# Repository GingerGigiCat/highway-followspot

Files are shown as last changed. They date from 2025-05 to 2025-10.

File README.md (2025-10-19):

# HIGHLIGHT!

## Highlight is my followspot i've designed for hack club's [highway](https://highway.hackclub.com/) hardware event



A **followspot** is a type of spotlight used in theatre which is manually controlled and pointed at an actor. They normally have brightness and zoom controls, which mine has!

It has:

- An over 100W white LED COB chip for over 17000 lumens of light output (Max. 150W, real max depends on how much heat the led dissipates as i'll have to limit it so it can't overheat and die)
- An upcycled camera lens no longer good enough for photography but perfect for a beam of light
- Motorised lens control with manual control if desired and zoom recall
- Digital constant current LED dimming (so no flickering from PWM)
- USB-C for computer control of brightness and zoom
- Fully open source everything
- 3 programmable buttons and a fader
- Automatic brightness reduction if the LED gets too hot
- A light on the control panel to give feedback, like if the main LED is too hot or the lens is being pushed too far

The body is 3D printed in PETG but it could be made out of a better material if you feel like it, and the legs are plywood, and of course the lens is glass.

Here's the onshape link! https://cad.onshape.com/documents/9e98bdcd2562c04de815ecc5/w/89c7868c82d5394c068b4491/e/8808e6d7c01ac629712aeab9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

## Why?

I wanted my GCSE Design and Technology project to be a spotlight, but my DT teacher said no and told me to downsize it to a desk lamp. It got me a good grade, but it's not what I wanted to make, so I'm taking the opportunity to make what I want to make, with an LED bright enough to blind my DT teacher! (/j....) I'm going to take inspiration from my project, as I do like the general hexagonal design of it (see below)

PXL_20250429_132238411 MP

I have a passion for the technical parts of theatre, so making this was rather an obvious choice for me

## PCB

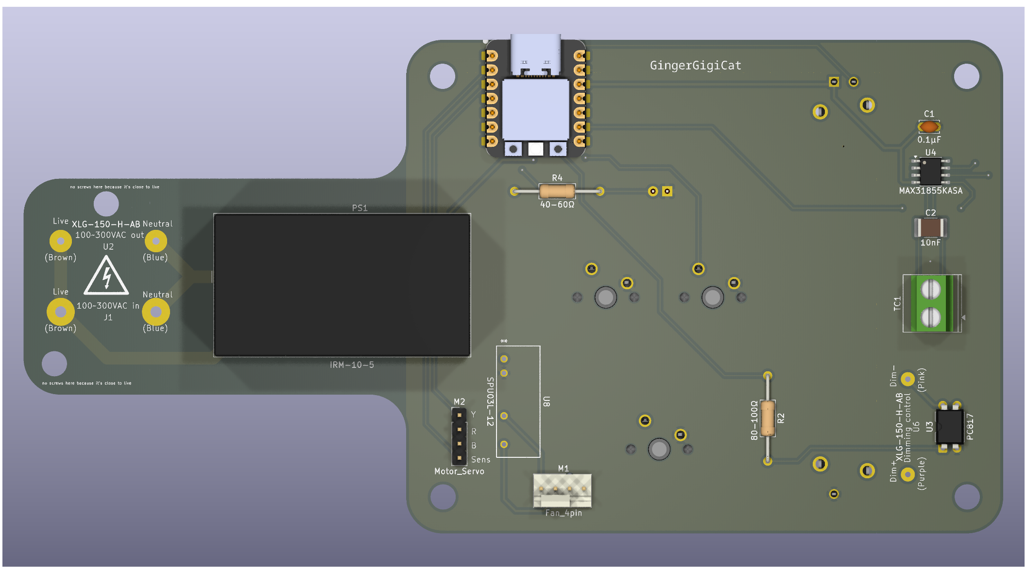
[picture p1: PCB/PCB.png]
PCB


## Wiring Diagram

(Made in GIMP :))

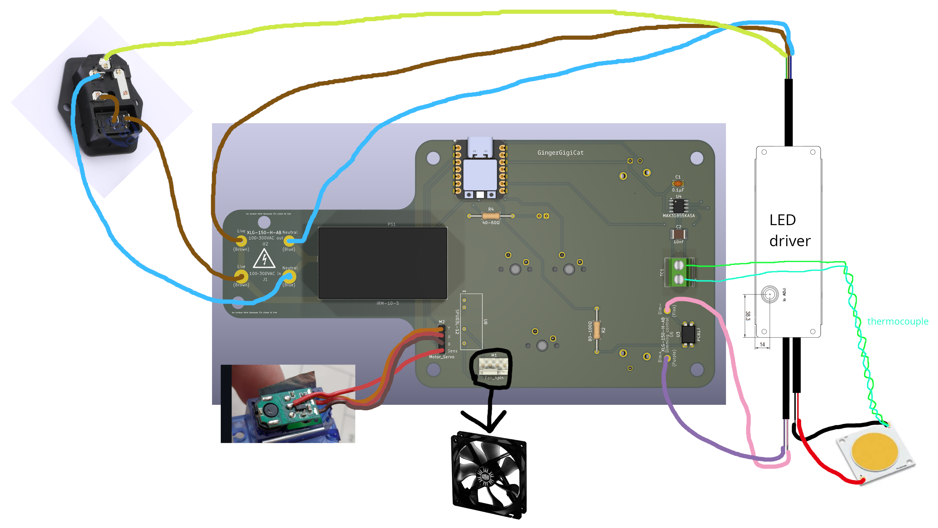
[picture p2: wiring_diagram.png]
wiring_diagram


## More pictures :)







overview_image_267752774_635424

# Bill of Materials

| Vendor | Name (link) | Description | Price (Digikey With VAT) | Price (Local) | Price (LCSC)  | Price(Other) | Notes |
| --- | --- | --- | --- | --- | --- | --- | --- |
| digikey | [XLG-150-H-AB ](https://www.digikey.co.uk/en/products/detail/mean-well-usa-inc/XLG-150-H-AB/10222586) | 150W 27-56V led driver | £31.04 | | x | | |
| LCSC | [IRM-10-5](https://lcsc.com/product-detail/Power-Module-Power-Supply_MW-MEAN-WELL-Enterprises-IRM-10-5_C2857903.html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) | 10W 5V psu | x 6.38 | | $4.32 | | |
| digikey | [SPU03L-12](https://www.digikey.co.uk/en/products/detail/mean-well-usa-inc/SPU03L-12/7707058) | 3W 5v to 12v conerter | £4.51 | | | | |
| digikey | [‎CXM-32-50-80-54-AC00-F2-5‎](https://www.digikey.co.uk/en/products/detail/luminus-devices-inc/CXM-32-50-80-54-AC00-F2-5/5811014) | 50-56V up to 200W LED | £21.78 | | x | | |
| digikey | [K104K15X7RF5TL2](https://www.digikey.co.uk/en/products/detail/vishay-beyschlag-draloric-bc-components/K104K15X7RF5TL2/286538) | 0.1uF tht capacitor | £0.22 | | | | |
| digikey | ["885012210006"](https://www.digikey.co.uk/en/products/detail/w%C3%BCrth-elektronik/885012210006/5453247) | 10nF smt capacitor | £0.46 | | | | |
| digikey | [PTA6043-2010CIB502](https://www.digikey.co.uk/en/products/detail/bourns-inc/PTA6043-2010CIB502/3781226) | 5K slide potentiometer | £1.70 | | x? | | |
| LCSC | [ETA-G-K-24-200cm](https://lcsc.com/product-detail/Electronic-testing-accessories_ETA-ETA-G-K-24-200cm_C5144202.html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) | 2m K-type thermocouple bare wires | | | $4.56 | | |
| LCSC | [MAX31855KASA+T](https://lcsc.com/product-detail/ADCs-DACs-Special-Purpose_Analog-Devices-Inc-Maxim-Integrated-MAX31855KASA-T_C52028.html) | MAX31855 thermocouple amplifier chip | x 8.28 | | $2.33 | | |
| digikey | [Wuerth elektronik screw pin terminal](https://www.digikey.co.uk/en/products/detail/w%C3%BCrth-elektronik/691137710002/6644051) | Screwy terminal block for 2 pins for thermocouple | £0.32 | | | | |
| digikey | [xiao rp2040](https://www.digikey.co.uk/en/products/detail/seeed-technology-co-ltd/102010428/14672129) | xiao rp2040 microcontroller | £4.15 | | x | | |
| digikey | [PC817X2NSZ9F](https://www.digikey.co.uk/en/products/detail/sharp-socle-technology/PC817X2NSZ9F/7942022) | pc817 optocoupler/optoisolator | £0.24 | | x $0.38=£0.28 | | (LCSC minimum order quantity is 5, for just one it would be $0.07 but alas) |
| | | 40 ohm resistor for led | (I have already) | | | £0.05 | (estimate price) |
| | | Red led | (I have already) | | | ~5p if you buy? | |
| | | 80-100 ohm resistor for optocoupler | (will get locally) | | | £0.05 | (estimate price) |
| | | 3x cherry style keyboard switches and keycaps | (I have already) | | | ~5p if you buy? | |
| | | 2.5A fuse - possibly 5x20mm | (will get locally) | | | £0.10 | (estimate price) |
| | | SG90 servo motor | (I have already) | | | | |
| LCSC | [Legion RT-C14B-H1+SS11-1BB](https://lcsc.com/product-detail/AC-Power-Connectors_Legion-RT-C14B-H1-SS11-1BB_C22379821.html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) | iec panel mount input with fuse and switch integrated | x 1.45 | | $1.46 | | LCSC one has a switch too! |
| digikey | [xiao pin headers](https://www.digikey.co.uk/en/products/detail/seeed-technology-co-ltd/102010490/19176770) | 7 pin headers for xiao rp2040, as well as for the servo | £0.22 | (might get locally) | | | |
| digikey | [molex 47053-1000](https://www.digikey.co.uk/en/products/detail/molex/0470531000/2421261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) | 4 pin fan header | £0.43 | | x | | |
| digikey | [ATS-HP-F9L200S70W-014](https://www.digikey.co.uk/en/products/detail/advanced-thermal-solutions-inc/ATS-HP-F9L200S70W-014/5049697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) | 200mm long 10.5mm wide ~60W heat pipe - 3 OF THEM | £12.90 | | | | |
| amazon | [1kg sunlu black petg filament](https://www.amazon.co.uk/SUNLU-Filament-Tangle-Free-Dimensional-Accuracy/dp/B0D1KC72YP) | 1kg black PETG sunlu filament, for more heat resistance | | | | £8.75 | (i'm splitting the cost with a friend so i only get 1kg and pay £8.75 for it, normally it would be about £12) |
| vinted | [Cooler master hyper 212 evo](https://www.vinted.co.uk/items/6787848360-coolmasters-hyper-212-fan) | heatsink with fan | | | | £9.71 |(previously fb marketplace but the one i was going to get sold) |
| amazon | [10g Silicone EC360 Thermal Glue](https://www.amazon.co.uk/EC360%C2%AE-Glue-Thermal-Adhesive-Liquid/dp/B00XQ9AZ8Y) | Thermally conductive adhesive for attaching heat pipes | | | | £5.99 | |
| | | 50x85mm 3mm mdf | | | | free | |
| | | about 40 m4 bolts and nuts (12mm long mostly but some might be longer) | | | | £6 | (estimate price) |
| | | 2 m10 bolts and nuts | | | | £6.00 | |
| | | about 400x200mm of thick plywood | | | | free | |
| JLCPCB | | The pcb!!! | | | | £12.00 | |
| | | | | | | | |
| | | | | | | | |
| | | | | | $12.45 | | Just parts cost |
| shipping stuff | | | | | $10.40 | | Shipping cost |
| Total | | | £78.18 | | $22.85=£16.73 | £48.94 | £144.25 |
| | | | | | cheaper! | | |
| Total total | (manual value input) | | | | | | $195.39 |

(I am willing to cover the amount i've gone over budget if i have to)

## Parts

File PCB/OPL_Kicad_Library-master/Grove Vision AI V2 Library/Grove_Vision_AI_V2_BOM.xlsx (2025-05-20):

Layer Jump | Number | Name | Specification | Operating Temperature | MPN Code | Quantity | Base | Plug Position | Process
N | 301010000 | SMD RES 0R-5%-1/16W;0402 |  | -55°C to 155°C | RC0402JR-070RL | 3 | 1 | R29,R30,R39 | SMT1
N | 301010004 | SMD RES 10K-5%-1/16W;0402 |  | -55°C to 155°C | RC0402JR-0710KL | 7 | 1 | R5,R7,R8,R23,R24,R31,R38 | SMT1
N | 301010008 | SMD RES 510K-5%-1/16W;0402 |  | -55°C to 155°C | RC0402JR-07510KL | 1 | 1 | R35 | SMT1
N | 301010456 | SMD RES 100K-1%-1/16W;0402 |  | -55°C to 155°C | RC0402FR-07100KL | 7 | 1 | R6,R10,R11,R16,R32,R33,R37 | SMT1
N | 301010495 | SMD RES;5.1K-1%-1/16W;0402 |  | -55°C to 155°C | RC0402FR-075K1L | 3 | 1 | R2,R3,R36 | SMT1
N | 301010746 | SMD RES 2.2K-1%-1/16W;0402 |  | -55°C to 155°C | RC0402FR-072K2L | 10 | 1 | R1,R4,R13,R14,R15,R19,R20,R21,R22,R40 | SMT1
N | 301011331 | SMD RES 22.1K-1%-1/16W;0402 |  | -55°C to 155°C | RC0402FR-0722K1L | 2 | 1 | R26,R34 | SMT1
N | 302010004 | SMD CAP Ceramic 100nF-16V-10%-X7R;0402 |  | -55°C to 125°C | CC0402KRX7R7BB104 | 18 | 1 | C5,C8,C13,C20,C21,C22,C23,C24,C25,C26,C27,C29,C30,C31,C32,C35,C36,C39 | SMT1
N | 302010006 | SMD CAP Ceramic 10nF-50V-10%-X7R;0402 |  | -55°C to 125°C | CC0402KRX7R9BB103 | 1 | 1 | C3 | SMT1
N | 302010049 | SMD CAP Ceramic 12pF-50V-5%-NPO;0402 |  | -55°C to 125°C | CC0402JRNPO9BN120 | 2 | 1 | C14,C15 | SMT1
N | 302010051 | SMD CAP Ceramic 220nF-16V-10%-X7R;0402 |  | -55°C to 125°C | CC0402KRX7R7BB224 | 1 | 1 | C16 | SMT1
N | 302010407 | SMD CAP Ceramic 4.7uF-10V-10%-X5R;0402 |  | -55°C to 85°C | CC0402KRX5R6BB475 | 7 | 1 | C4,C6,C7,C9,C10,C28,C34 | SMT1
N | 302010519 | SMD CAP Ceramic 10uF-10V-20%-X5R;0402 |  | -55°C to 85°C | CC0402MRX5R6BB106 | 2 | 1 | C11,C37 | SMT1
N | 302013249 | SMD CAP Ceramic 1uF-10V-10%-X5R;0402 |  | -55°C to 85°C | CL05A105KP5NNNC | 5 | 1 | C1,C2,C17,C18,C19 | SMT1
N | 303010544 | SMD Inductor 4.7uH-20%-1.1A;0806 |  | -40°C to 105°C | VLS201610HBX-4R7M-1 | 1 | 1 | L1 | SMT1
N | 303011858 | SMD Inductor 470nH-20%-2.6A;0603 |  | -40°C to 125°C | TFM160808ALC-R47MTAA | 2 | 1 | L2,L3 | SMT1
N | 304011053 | SMD Diode Schottky 40V-1A;SOD-323 |  |  | B5819WS SL | 4 | 1 | D1,D2,D3,D4 | SMT1
N | 304090121 | SMD LED Clear-Green;0402 | As posted |  | BL-HGE37A-AV-TRB | 1 | 1 | LED2 | SMT1
N | 304090746 | SMD LED Clear-Yellow;0402 | As posted |  | 16-213/Y2C-AN2Q1B/3T | 1 | 1 | LED1 | SMT1
N | 305030071 | SMD MOSFET N-CH 20V-500mA;SOT-523 |  |  | CJ1012 | 5 | 1 | Q1,Q2,Q3,Q4,Q5 | SMT1
N | 306011444 | SMD Crystal;24MHz-12pF-10ppm-4P-2.0*1.6*0.5mm |  | -40°C to 85°C | Y2400FE001 | 1 | 1 | X1 | SMT1
N | 310011697 | SMD IC MCU;Dual Cortex-M55 Core(Max 400MHz)-With a 400MHz NPU;WLCSP-65 | L5.58*W2.27mm | -40°C to 85°C | HX6538-A01TWA | 1 | 1 | U1 | SMT1
N | 310032794 | SMD IC PMIC;DCDC Buck-ADJ-2.2MHz-4A;DFN1.5×1.5-6 |  | -40°C to 85°C | SY80004DQD | 2 | 1 | U4,U6 | SMT1
N | 310032813 | SMD IC PMIC;LDO-1.8V-300mA;XTDFN-1*1-4L |  | -40°C to 125°C | SGM2036S-1.8XXDH4G/TR | 1 | 1 | U3 | SMT1
N | 310071431 | SMD IC Interface USB to High Speed TTL;QFN16 | USB to High-Speed Serial Port | -40°C to 85°C | CH343P | 1 | 1 | U2 | SMT1
N | 310091468 | SMD IC Memory;128Mbit-1.8V;SOIC-8 |  | -40°C to 85°C | W25Q128JWSIQ | 1 | 1 | U5 | SMT1
N | 311020009 | SMD Top Button 4N;4P-L4.6*W3.2*H2.5mm |  | -20°C to 70°C | SKRPADE010 | 1 | 1 | RST1 | SMT1
N | 311020518 | SMD Top Button 1.57N;4P-L4.6*W3.2*H2.5mm |  | -30°C to 85°C | SKRPABE010 | 1 | 1 | BOOT1 | SMT1
N | 312030502 | SMD DIGITAL MIC OMNI -26dBFS;OCLGA-4:3.5*2.65*0.94mm |  | -40˚C to 100˚C | MSM261D3526H1CPM | 1 | 1 | MIC1 | SMT1
N | 319015667 | PCB;Grove - Vision AI Module V2 -蓝油白字-4层 | 20*40*1.6mm-ENIG-FR4;Steel mesh code；404012305 |  |  | 1 | 1 |  | SMT1
N | 320011358 | SMD USB TYPE C-W/P;12+4P-8.94*7.35*3.26mm |  | -30°C to 85°C | USB-31C-F-16P-L7.35 | 1 | 1 | J1 | SMT1
N | 320031231 | DIP Black Female Header VERT;1*7P-2.54-5.0mm |  | -40℃ to 105℃ |  | 2 | 1 | P8,P9 | Unit
N | 320060904 | SMD FPC CONN Bottom Contact;15P-1.0mm;L19.9*W6.76*H2.0mm |  | -30°C to 85°C | ST-FPC-W102015-D | 1 | 1 | J2 | SMT1
N | 320090535 | SMD uSD Card Holder;9+4P-L11.25*W6.96*H1.42mm |  | -25°C to 70°C | ST-TF-MR267 | 1 | 1 | J5 | SMT1
N | 320110032 | SMD Grove Female Header-Beige;4P-2.0-90D | 2.0-4PHorizontal Mount with Locking Socket |  | PHS-4A horizontal mount | 1 | 1 | J3 | SMT1

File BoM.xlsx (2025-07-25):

Vendor | Name (link) | Description | Price (Digikey With VAT) | Price (Local) | Price (LCSC) | Price(Other) | Notes
~~digikey~~ | ~~ELG-150-54B~~ (https://www.digikey.co.uk/en/products/detail/mean-well-usa-inc/ELG-150-54B/7702975) | ~~150W 54V led driver~~ | ~~x 37.94~~ |  | ~~x~~ |  | ~~BACKORDER NEEDS BUYING, LEAD TIME CURRENTLY 13/06/2025~~
digikey | XLG-150-H-AB (https://www.digikey.co.uk/en/products/detail/mean-well-usa-inc/XLG-150-H-AB/10222586) | 150W 27-56V led driver | £31.04 |  | x
LCSC | IRM-10-5 (https://www.digikey.co.uk/en/products/detail/mean-well-usa-inc/IRM-10-5/7704657) | 10W 5V psu | x 6.38 |  | $4.32 (https://lcsc.com/product-detail/Power-Module-Power-Supply_MW-MEAN-WELL-Enterprises-IRM-10-5_C2857903.html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)
~~digikey~~ | ~~SMU02L-12~~ (https://www.digikey.co.uk/en/products/detail/mean-well-usa-inc/SMU02L-12/7706871) | ~~2W 5v to 12v converter~~ | ~~x 3.54~~ |  | ~~x?~~
digikey | SPU03L-12 (https://www.digikey.co.uk/en/products/detail/mean-well-usa-inc/SPU03L-12/7707058) | 3W 5v to 12v conerter | £4.51
digikey | L2C5-40801825G3200 (https://www.digikey.co.uk/en/products/detail/lumileds/L2C5-40801825G3200/7344822) | 51.7V ~116W LED | £34.15 |  | x
~~digikey~~ | ~~Schurter OGN Fuse holder~~ (https://www.digikey.co.uk/en/products/detail/schurter-inc/0031-8211/669926) | ~~5x20mm fuse holder~~ | ~~x 1.04~~ |  | ~~x?~~
digikey | K104K15X7RF5TL2 (https://www.digikey.co.uk/en/products/detail/vishay-beyschlag-draloric-bc-components/K104K15X7RF5TL2/286538) | 0.1uF tht capacitor | £0.22
digikey | "885012210006" (https://www.digikey.co.uk/en/products/detail/w%C3%BCrth-elektronik/885012210006/5453247) | 10nF smt capacitor | £0.46
digikey | PTA6043-2010CIB502 (https://www.digikey.co.uk/en/products/detail/bourns-inc/PTA6043-2010CIB502/3781226) | 5K slide potentiometer | £1.70 |  | x?
~~digikey~~ | ~~240-080~~ (https://www.digikey.co.uk/en/products/detail/digilent-inc/240-080/5418219) | ~~1m K-type thermocouple bare wires~~ | ~~x 8.86~~ |  | ~~x~~
LCSC | ETA-G-K-24-200cm (https://lcsc.com/product-detail/Electronic-testing-accessories_ETA-ETA-G-K-24-200cm_C5144202.html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) | 2m K-type thermocouple bare wires |  |  | $4.56 (https://lcsc.com/product-detail/Electronic-testing-accessories_ETA-ETA-G-K-24-200cm_C5144202.html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)
LCSC | MAX31855KASA+T (https://www.digikey.co.uk/en/products/detail/analog-devices-inc-maxim-integrated/MAX31855KASA-T/2591213) | MAX31855 thermocouple amplifier chip | x 8.28 |  | $2.33 (https://lcsc.com/product-detail/ADCs-DACs-Special-Purpose_Analog-Devices-Inc-Maxim-Integrated-MAX31855KASA-T_C52028.html)
digikey | Wuerth elektronik screw pin terminal (https://www.digikey.co.uk/en/products/detail/w%C3%BCrth-elektronik/691137710002/6644051) | Screwy terminal block for 2 pins for thermocouple | £0.32
digikey | xiao rp2040 (https://www.digikey.co.uk/en/products/detail/seeed-technology-co-ltd/102010428/14672129) | xiao rp2040 microcontroller | £4.15 |  | x
digikey | PC817X2NSZ9F (https://www.digikey.co.uk/en/products/detail/sharp-socle-technology/PC817X2NSZ9F/7942022) | pc817 optocoupler/optoisolator | £0.24 |  | x $0.38=£0.28 |  | (LCSC minimum order quantity is 5, for just one it would be $0.07 but alas)
 |  | 40 ohm resistor for led | (I have already) |  |  | £0.05 | (estimate price)
 |  | Red led | (I have already) |  |  | ~~~5p if you buy?~~
 |  | 80-100 ohm resistor for optocoupler | (will get locally) |  |  | £0.05 | (estimate price)
 |  | 3x cherry style keyboard switches and keycaps | (I have already) |  |  | ~~~5p if you buy?~~
 |  | 2.5A fuse - possibly 5x20mm | (will get locally) |  |  | £0.10 | (estimate price)
 |  | SG90 servo motor | (I have already)
LCSC | DAC-13F (https://www.digikey.co.uk/en/products/detail/dit/DAC-13F/18681314) | iec panel mount input with fuse integrated | x 1.45 |  | $1.46 (https://lcsc.com/product-detail/AC-Power-Connectors_Legion-RT-C14B-H1-SS11-1BB_C22379821.html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) |  | LCSC one has a switch too!
digikey | xiao pin headers (https://www.digikey.co.uk/en/products/detail/seeed-technology-co-ltd/102010490/19176770) | 7 pin headers for xiao rp2040, as well as for the servo | £0.22 | (might get locally)
digikey | molex 47053-1000 (https://www.digikey.co.uk/en/products/detail/molex/0470531000/2421261) | 4 pin fan header | £0.43 |  | x
digikey | ATS-HP-F9L200S70W-014 (https://www.digikey.co.uk/en/products/detail/advanced-thermal-solutions-inc/ATS-HP-F9L200S70W-014/5049697) | 200mm long 10.5mm wide ~60W heat pipe - 3 OF THEM | £12.90
~~AMAZON~~ | ~~1kg Creality Black PETG filament~~ (https://www.amazon.co.uk/Creality-PETG-Filament-1-75-Printer/dp/B0DZVWW11M) | ~~1kg black PETG creality filament, i need it for the better heat resistance~~ |  |  |  | ~~x 12.99~~ (https://www.amazon.co.uk/Creality-PETG-Filament-1-75-Printer/dp/B0DZVWW11M)
amazon | 1kg sunlu black petg filament (https://www.amazon.co.uk/SUNLU-Filament-Tangle-Free-Dimensional-Accuracy/dp/B07TJDTJZD) | 1kg black PETG sunlu filament, for more heat resistance |  |  |  | £8.75 (https://www.amazon.co.uk/SUNLU-Filament-Tangle-Free-Dimensional-Accuracy/dp/B0D1KC72YP) | (i'm splitting the cost with a friend so i only get 1kg and pay £8.75 for it, normally it would be about £12)
fb marketplace | Cooler master hyper 212 evo (https://www.facebook.com/marketplace/item/1101663772011711) | heatsink with fan |  |  |  | £10.00
amazon | 10g Silicone EC360 Thermal Glue (https://www.amazon.co.uk/EC360%C2%AE-Glue-Thermal-Adhesive-Liquid/dp/B00XQ9AZ8Y) | Thermally conductive adhesive for attaching heat pipes |  |  |  | £5.99
 |  | 50x85mm 3mm mdf |  |  |  | free
 |  | about 40 m4 bolts and nuts (12mm long mostly but some might be longer) |  |  |  | £6 | (estimate price)
 |  | 2 m10 bolts and nuts |  |  |  | £6.00
 |  | about 400x200mm of thick plywood |  |  |  | free
JLCPCB |  | The pcb!!! |  |  |  | £12.00
 |  |  |  |  | $12.45 |  | Just parts cost
shipping stuff |  |  |  |  | $10.40 |  | Shipping cost
Total |  |  | £90.34 |  | $22.85=£16.73 | £48.94 | £156.01
 |  |  |  |  | cheaper!
Total total | (manual value input) |  |  |  |  |  | $209.51

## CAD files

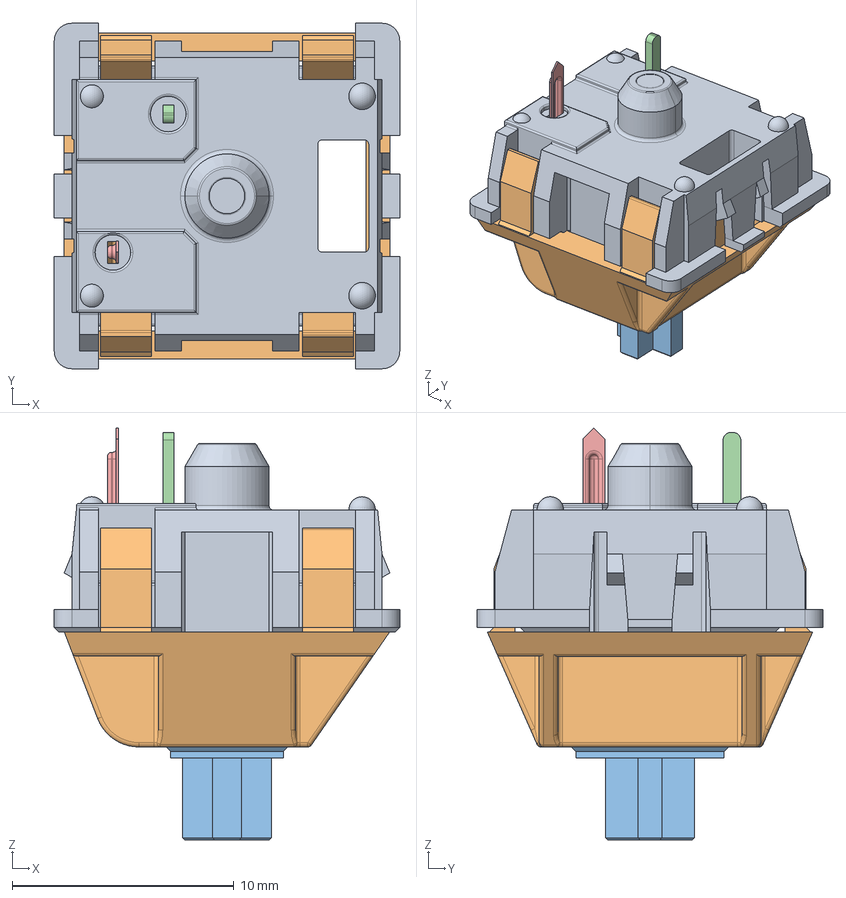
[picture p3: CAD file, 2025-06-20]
PCB/3d_models/cherry_switch.stp
15.6 x 15.6 x 18.6 mm
MX_DOWN
MX_UP
UP_MX
MX_PIN
MX_SPRING
MX_CLICK

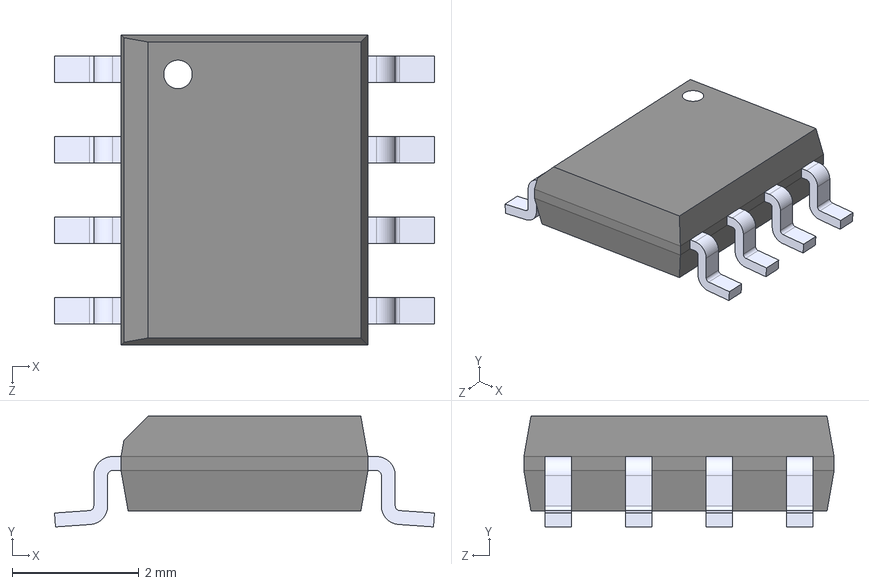
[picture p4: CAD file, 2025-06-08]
PCB/MAX6675/MAX6675.step
6.00 x 1.75 x 4.90 mm

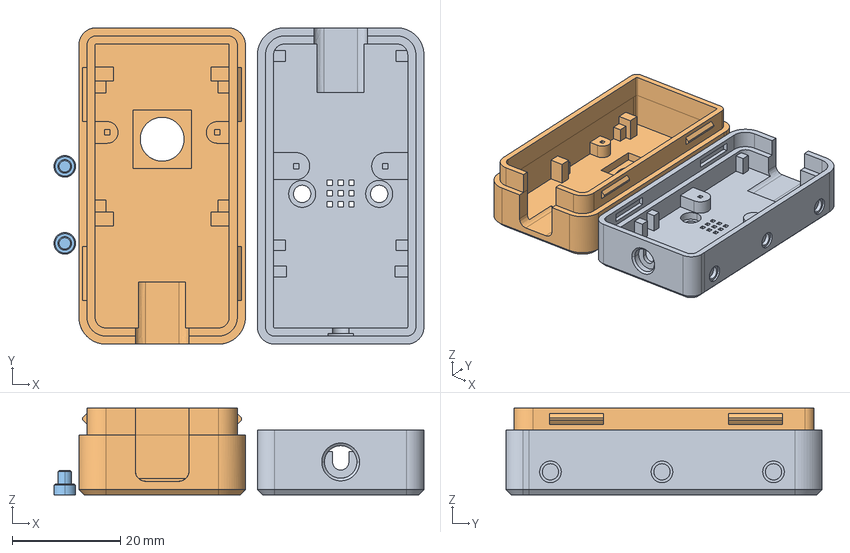
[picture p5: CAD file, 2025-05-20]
PCB/OPL_Kicad_Library-master/Grove Vision AI V2 Library/himax.stp
68.4 x 58.5 x 16.1 mm

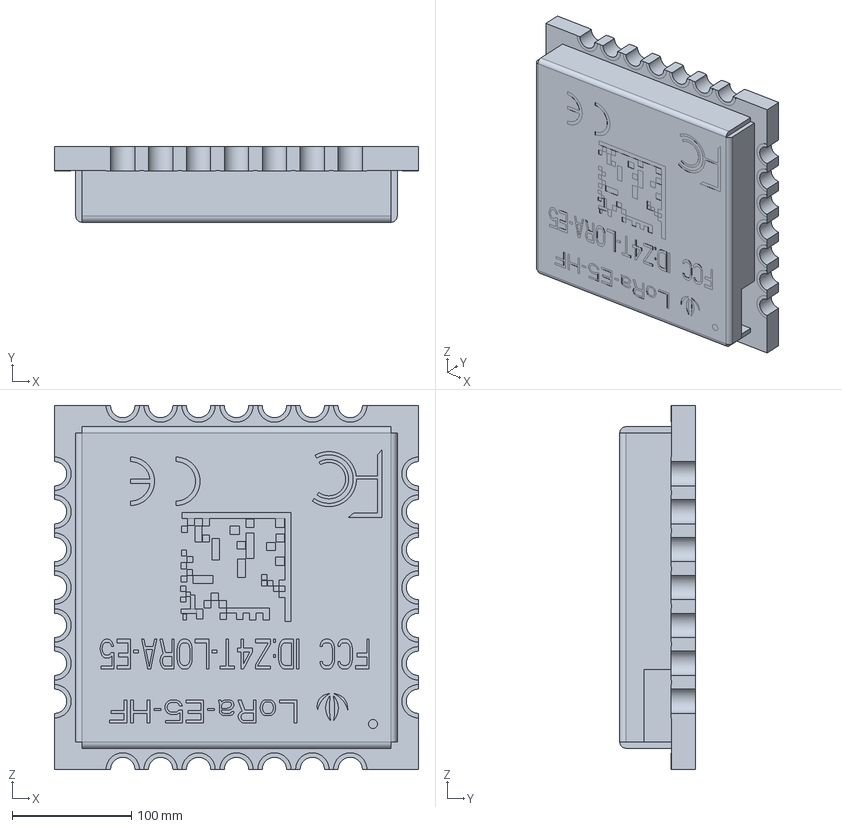
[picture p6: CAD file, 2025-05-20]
PCB/OPL_Kicad_Library-master/Seeed Studio Wio Series/Wio-E5-LE/LoRa-E5-LE-HF_3D_File.stp
304.8 x 63.8 x 304.8 mm

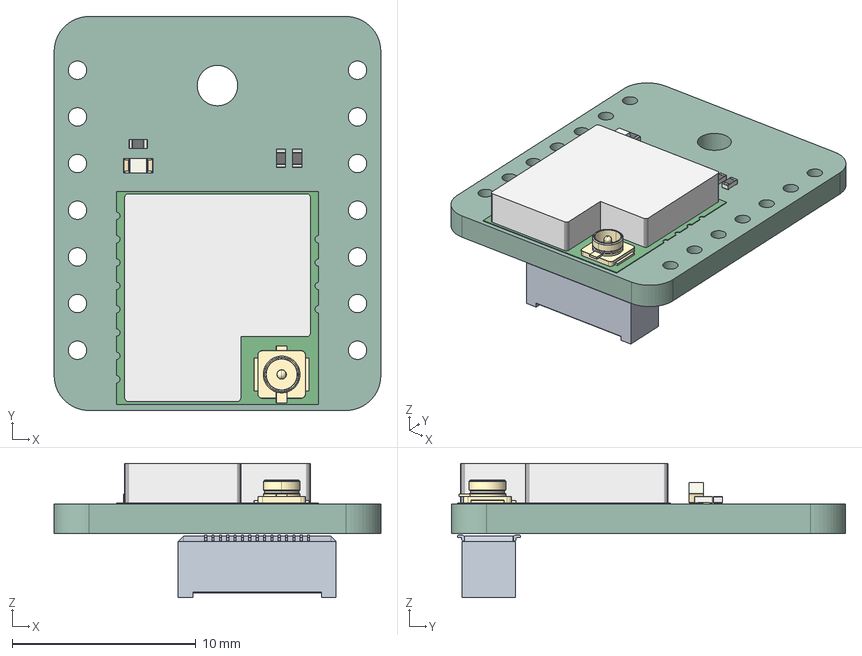
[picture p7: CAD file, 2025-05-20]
PCB/OPL_Kicad_Library-master/Seeed Studio Wio Series/Wio-SX1262/Wio-SX1262_for_XIAO_3D_file.step
17.8 x 21.4 x 7.30 mm
R_0402_1005Metric x 3
LED_0603_1608Metric
PCB
BF04-30pin-35H
Wio-SX1262 for XIAO V1.0_PCB

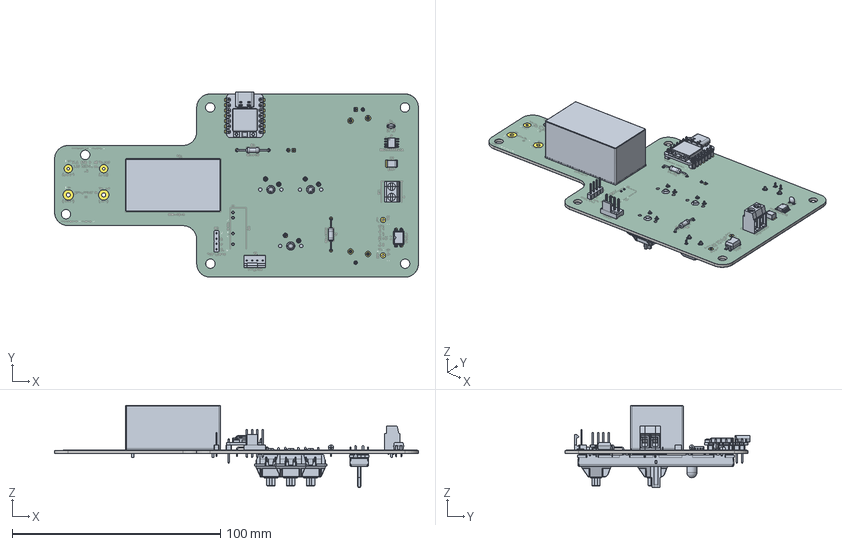
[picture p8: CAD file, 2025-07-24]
PCB/PCB.step
174.8 x 89.0 x 39.5 mm
SOIC-8_3.9x4.9mm_P1.27mm
DIP-4_W7.62mm
R_Axial_DIN0207_L6.3mm_D2.5mm_P15.24mm_Horizontal x 2
C_1812_4532Metric
PinHeader_1x04_P2.54mm_Vertical
FanPinHeader_1x04_P2.54mm_Vertical
MRT12P5_SX
MRT12P5_CNT
MRT12P5_DX
power_supply_irm-10-5
C_Disc_D3.4mm_W2.1mm_P2.50mm
7-Pin Header - Male - 2.54mm x 2
MX_DOWN x 3
MX_UP x 3
UP_MX x 3
MX_PIN x 3
MX_SPRING x 3
MX_CLICK x 3
LED_D5.0mm
PCB_copper
PCB_silkscreen
PCB_soldermask
PCB_PCB

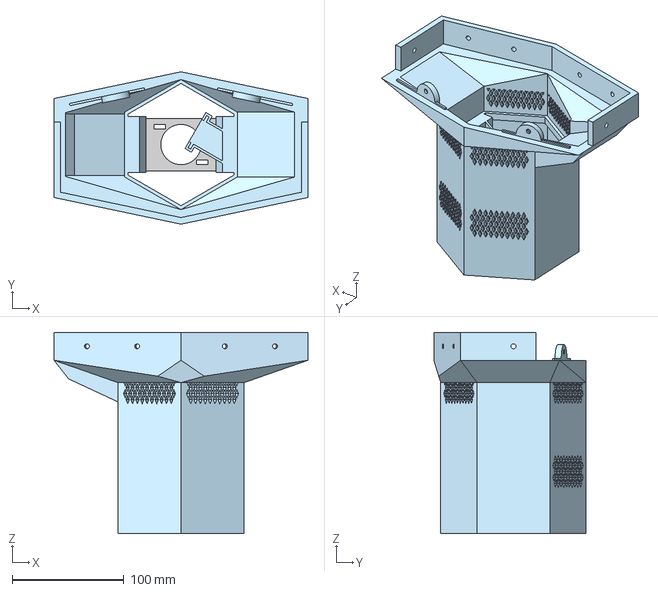
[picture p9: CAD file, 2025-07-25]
Production/3d print parts/Outer Light Tube.step
227.0 x 136.2 x 180.0 mm

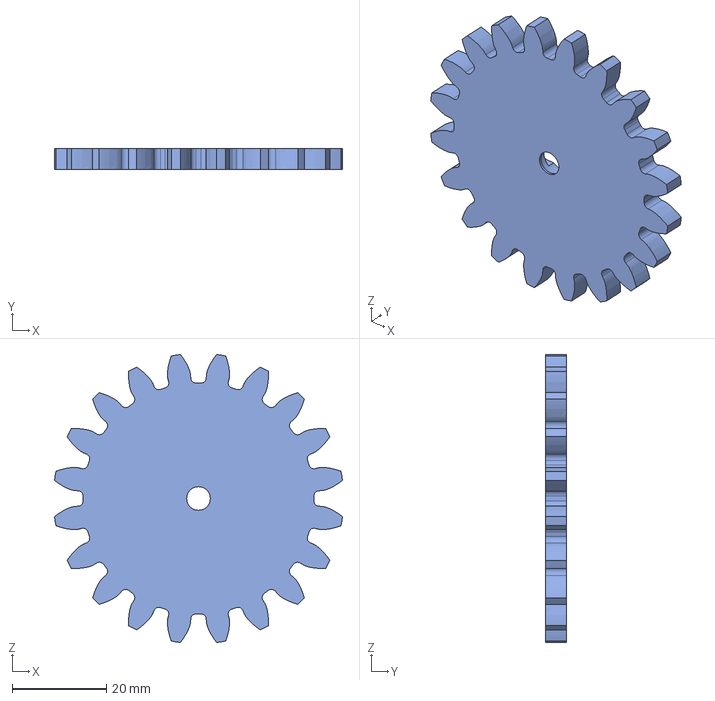
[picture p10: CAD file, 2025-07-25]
Production/3d print parts/Gear.step
61.1 x 4.50 x 61.1 mm

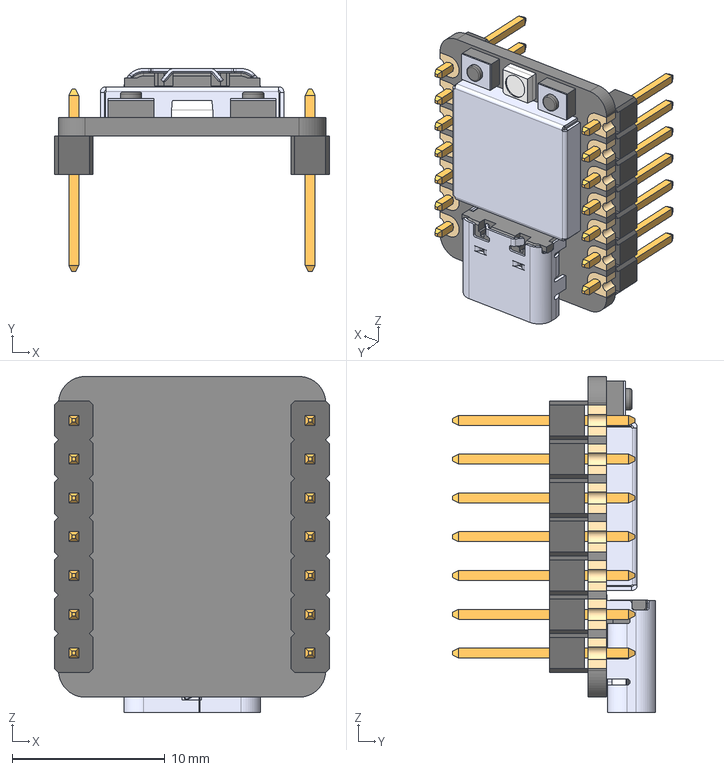
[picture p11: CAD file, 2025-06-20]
PCB/3d_models/xiao rp2040 with pins.step
18.0 x 13.3 x 22.0 mm
7-Pin Header - Male - 2.54mm x 2

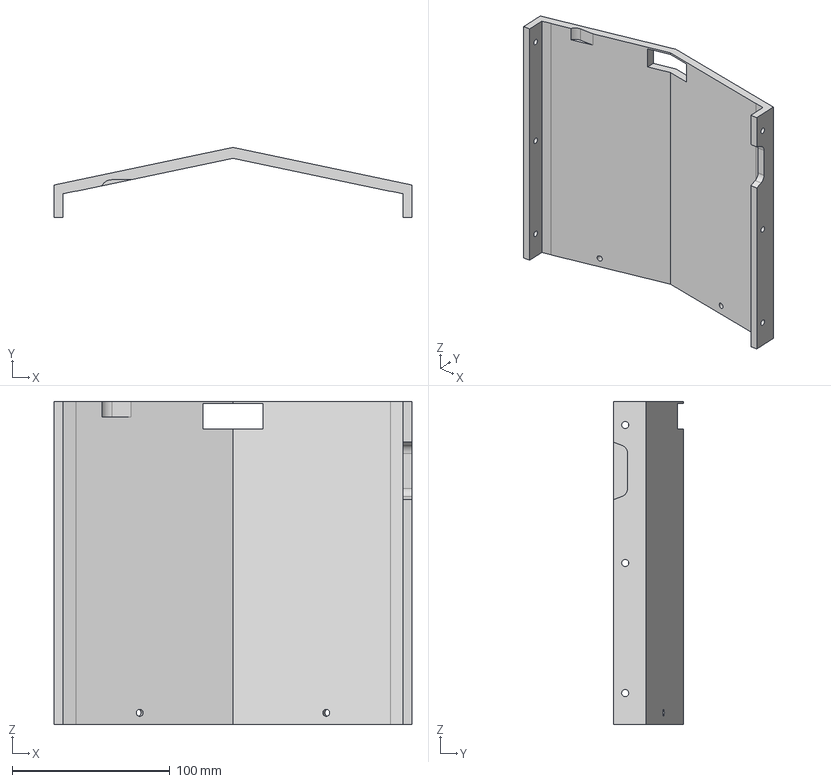
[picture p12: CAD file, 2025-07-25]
Production/3d print parts/electronics box roof.step
227.0 x 44.5 x 205.0 mm

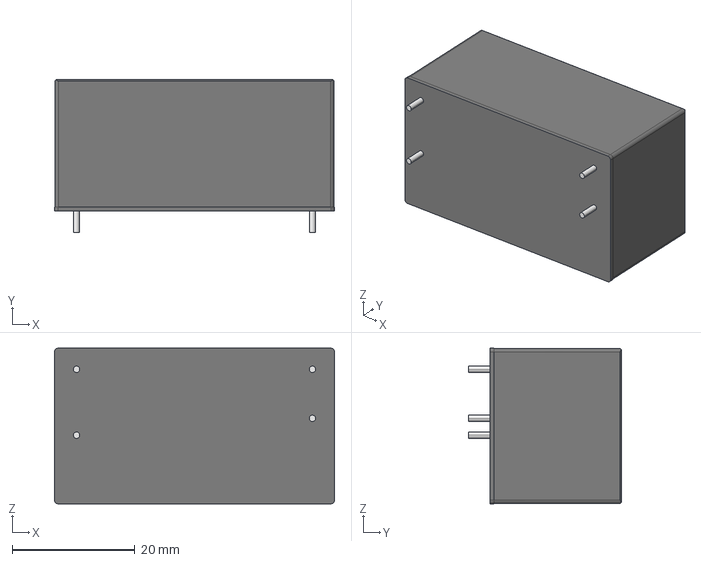
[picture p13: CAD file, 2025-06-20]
PCB/3d_models/power_supply_irm-10-5.stp
45.7 x 25.0 x 25.4 mm

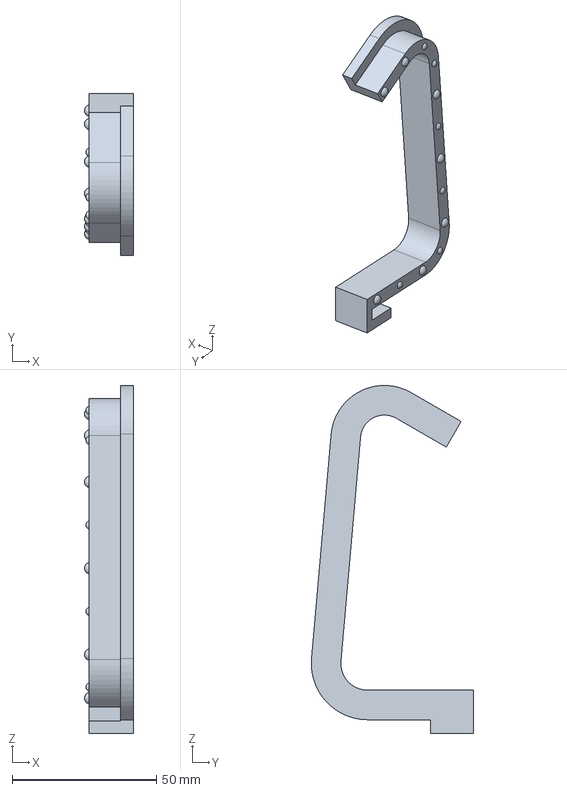
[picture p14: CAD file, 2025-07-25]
Production/3d print parts/pipe bending tool1 part1.step
17.0 x 56.2 x 120.4 mm

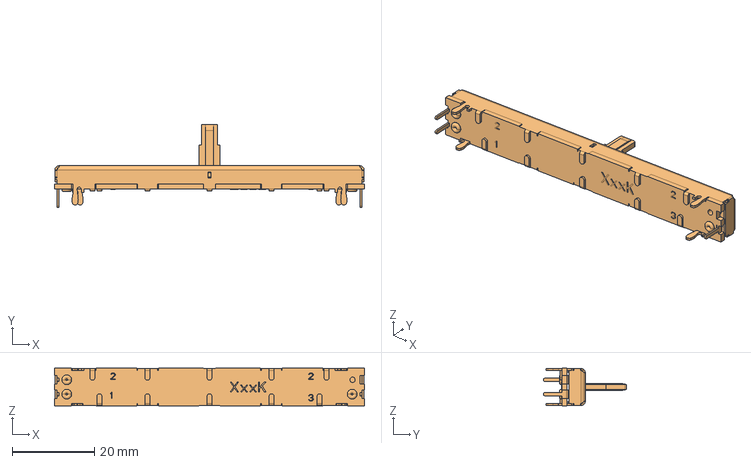
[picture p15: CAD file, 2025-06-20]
PCB/3d_models/pta6043-2x10cixxxx-fader.stp
75.2 x 20.2 x 9.20 mm

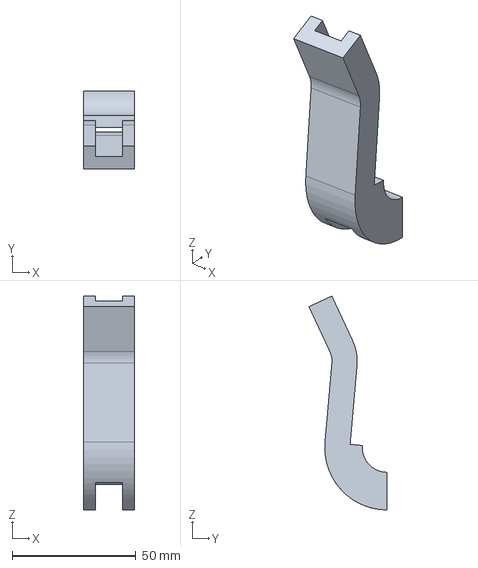
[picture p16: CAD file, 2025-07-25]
Production/3d print parts/pipe bending tool2.step
20.5 x 31.6 x 86.6 mm

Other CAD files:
PCB/3d_models/xiao rp2040 (no pins).STEP
Production/3d print parts/Inner Light Tube.step
Production/3d print parts/leg knob x2.step
PCB/3d_models/691137710002+%28rev1%29 terminal block.stp
PCB/OPL_Kicad_Library-master/Grove Vision AI V2 Library/himax.3mf
Production/3d print parts/Electronics Box.step
Production/3d print parts/Front handle.step
Production/3d print parts/Pinion.step
Production/3d print parts/back panel.step
Production/3d print parts/heatsink bracket x2.step
Production/3d print parts/pipe bending tool1 part2.step

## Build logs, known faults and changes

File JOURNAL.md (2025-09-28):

## Time so far: 3 + 1 + 2.5 + 1.5 + 1 + 3 + 1 + 4 + 2 + 1 + 1.5 + 3 + 3.5 + 0.5 + 0.25 + 1.25 + 4 + 0.5 + 1 + 1.5 + 1 + 1 + 0.5 + 2 + 4 + 1.5 + 2 + 2.5 + 4 + 1 + 2 + 1 + 1.5 + 2 = 65 hours

# Saturday 17 May 2025 - 19:00 - 3 hours

So I've been wanting to make a spotlight for a while. I had planned for my GCSE Design & Technology project to be a spotlight, so I did research including a questionnaire on what people look for in a spotlight, and I upcycled a camera lens which is unsuitable for a camera but it works great to put light through. However, my teacher decided no and told me to make a desk lamp in the style of a spotlight. No lens, no very bright LED, and nothing over 9V. And it got me a good grade, but it's underwhelming and it isn't what I wanted to make.

Therefore, I want to properly go through with designing and creating a real, bright, functioning spotlight, taking inspiration from my desk lamp (the desk lamp is below)

PXL_20250429_132217899 MP
PXL_20250501_122556802 MP

I am also inspired by the [beacon](https://hackclub.slack.com/archives/C0266FRGV/p1723503357605259) that [ruckusmatter](https://hackclub.slack.com/team/U06TZK6EKU6) made during arcade, and i'd like it include a way for my spotlight to have a perfectly straight beam. For reference, the beacon is 17,000 lumens and its colour temperature is 5600k.


Oh also, the 9/11 memorial [Tribute In Light](https://en.wikipedia.org/wiki/Tribute_in_Light) also inspired me

I've been researching LEDs and PSUs. I've been looking on mouser electronics, and I found 2 LEDs that particularly stand out to me.
[One of them](https://www.mouser.co.uk/ProductDetail/Cree-LED/CMB3090-R050-000Q0H0A40G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) is by CREE, a well-known and reliable LED manufacturer, so I should be able to rely on it. This one is 48V, which is nice as it is a rather common voltage, and it produces 12,488 lumens and has a colour temperature of 4000k, which is a more pleasant, warmer shade of white than the spotlight. However, I am unsure about this LED as not only is it less bright than the beacon, it also has some conflicting information as it says  it is 1.2A, but that it is 82W, which can not both be true with a voltage of 48V.

[This other LED](https://www.mouser.co.uk/ProductDetail/Lumileds/L2C5-40801825G3200?qs=T3oQrply3y8Ak6%2FCD8N%252BaQ%3D%3D), by Lumileds seems like it could be better. It is 51.7V at 2.25A and 116W, producing 17,075 lumens, with the same 4000k colour temperature. It should be very bright, however I don't know if it would be the same true light output as the beacon because of the potential for light loss, especially since the lens will have to be a distance away from the light in order to get a straight beam. However, the higher power requirements and weird voltage means finding a suitable power supply may be more difficult.

In terms of powering the LED, I was initially planning to just have a dc power supply of the needed voltage, then allow dimming the LED by using pwm with a MOSFET. I learned that using PWM might not be the best idea though with that much power. Instead a constant current dimmable LED power supply, like [this one](https://www.mouser.co.uk/ProductDetail/MEAN-WELL/ELG-100-48B?qs=n51ddIYULBkC86Em3tr4DQ%3D%3D) from the reputable power supply brand Mean Well. It's got 2 pins which are used for dimming, with 3 options for how to dim the LED. It can be done by: giving it a constant voltage from 0-10V, giving it PWM at 10V, and applying a resistance between the two pins. I'm not sure which of these is the best option, as I don't know of a microcontroller that can produce pwm at 10V, or give a constant variable voltage as high as 10V. This is something I will need to think about.

I would like to have motor controlled zooming of the lens, but I would also like to have the option to control it manually when I want to. For example, it would be great if I could just press a button and have the lens snap into place to give a perfectly straight beam, and be able to save a certain beam angle to repeat later. But also, when manually using it as a followspot, it can be much more convenient and intuitive to physically move a handle which moves the lens. Perhaps I could do this using the same kind of thing as how the extruder on my 3d printer is moved, I think using a belt. It can be moved freely by hand when it's off, but when it's on it is locked in place and I can't move it.

# Monday 19 May 13:00 - 1 hour

I was looking into how I would control the brightness. I was initially thinking I would need 3 power supplies in total, one for the microcontroller, one for the 10V PWM signal, and the LED driver. I thought I would have to use a MOSFET or transistor in order to control the PWM. However I then searched for how to dim a meanwell led driver in particular, and i found [this forum answer](https://electronics.stackexchange.com/a/563669) where they suggest using an optocoupler, which apparently works. An optocoupler is a small box for electrically isolating two circuits, containing an LED and a light dependent resistor. When the LED turns on, the LDR lets current 
 through on the other side. Therefore I can generate a PWM signal for the brightness, and it can go into the optocoupler and from the optocoupler into the dimming pins of the LED driver. I will need to look at the datasheet of the optocoupler I choose, to check the voltage and current needed so that I can choose the correct resistor value, as too much current will kill the LED inside.

I also thought a bit more about how I'm going to move the lens. I think I will house the lens in a tube inside the outer tube, and then move that tube in and out of the outer tube. I think this could be digitally controlled by using potentially a servo and a rack and pinion (image below) to convert the rotary movement of the servo into a linear movement of the tube. It would be good if the servo includes an encoder, so I can find what rotation the servo is at. Using that data I could then include code to compensate for how the brightness of the beam changes when the lens is moved, because as the lens is moved closer to the focal point, the beam gets brighter, which may not be wanted in some situations.

# Monday 19 May 16:00-17:30  18:00-18:30  19:00-19:30 - 2.5 hours

:( Edge decided my github tab is unimportant, so got rid of what i had typed here initially. I've been attempting to use kicad to start making, and it's not easy but i'm figuring it out. Oh also I realised that my school's solidworks licence runs out in like 4 days so I'm going to have to learn a completely different cad software :heavysob:. So I was at first trying to put an esp32-s2 on my pcb, but then things quickly got confusing because I realised I'd have to do power supply circuitry and clock timing and waaaaaaaaaaaaa so instead I thought I'd look at the hackpad tutorial, and i saw that it used the xiao-rp2040-dip, so I'm going to use it. It has all the pins i need, and it seems like it should be nice and simple to use. I am thinking about how to power the microcontroller, because I will have an AC input going to the LED driver, and I will need another power supply for the microcontroller. I found [this](https://www.hlktech.net/index.php?id=134) cute little AC to 5V DC converter, the part number is HLK-10M05. It will need a fuse, capacitor and resistor as well, but it should in theory do a lot of the work for me. I don't want to have two different cables plugged into my light, one for the microcontroller and one for the LED driver, so I believe this should work. I think I can just take two psus off of the same ac line? At this point I'm just getting a hold of kicad and working out the general idea of my schematic.



# Tuesday 20 May 17:30-18:00  19:00-19:30  21:15-21:45 - 1.5 hours
I asked [#electronics](https://hackclub.slack.com/archives/C056AMWSFKJ/p1747758821959079) in slack about how i'd power both the led driver, and after consulting with [Aiden](https://hackclub.slack.com/team/U06CHEJ7P6U) in [this](https://hackclub.slack.com/archives/C056AMWSFKJ/p1747758821959079) thread, and drawing the below, beautiful drawing, I came to the conclusion that it is safe to 
split the ac input to a 5v psu and the led driver. I'll use a standalone psu rather than making my own, perhaps I'll take apart some random cheap usb plug for it.


So, the more powerful LED ([this one](https://www.mouser.co.uk/ProductDetail/Lumileds/L2C5-40801825G3200?qs=T3oQrply3y8Ak6%2FCD8N%252BaQ%3D%3D)) is 51.7V. That's weird. But the minimum voltage is 48.8V and the maximum 56.3V, so that gives me some leeway to find a suitable driver for it. Unfortunately the minimum is a smidge higher than the voltage of the meanwell driver I had been looking at. I just found [this](https://www.mouser.co.uk/ProductDetail/MEAN-WELL/ELG-150-54B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) meanwell LED driver which looks great, it's 54V so should be within the suitable voltage range for the LED, and it's 150W to go with the 115W LED, so it won't always be running at 100%. And it's only £35 which is close to the old one! and of course it supports the same way of dimming.

Ok, after [@Parker Rupe](https://hackclub.slack.com/team/U08SPJPNKDZ)'s input, I'm not going to take apart some random usb plug, instead I'm going to use [this](https://www.mouser.co.uk/ProductDetail/MEAN-WELL/IRM-10-5?qs=WkdRfq4wf1Mbq1AdfDJBoQ%3D%3D) 5V 10W meanwell power supply, model IRM-10-5 [(datasheet)](https://www.meanwellusa.com/webapp/product/search.aspx?prod=IRM-10). I believe I can just slap it on and stick 240Vac into it, then it will give me 5V that can go into the xiao. Of course, I'm going to ask if someone who knows what they're doing (not me) can check over everything i design.
So now the ~~PCB~~ *schematic* looks like this (it looks like less than before...):



# Wednesday 21 May 10:15-10:45  18:30-19:00 - 1 hour
I've been getting the schematic good (I think) and i calculated what are apparently appropriate resistors, according to internet. Behold:



I haven't yet added a potentiometer and the motor for lens movement yet. I really don't know how I'm going to do the lens movement. I also don't know what I'm going to do with all the heat the led produces. I'll have to have a heatsink with a fan, maybe a proper cpu type cooler. I'll probably print the actual thing out of PETG, as it might be heat resistant.

# Thursday 22 May - 3 hours

I started learning onshape because my school's solidworks license expires soon!

I started modelling the lamp, as seen below, but then i decided it would be helpful to have a model (below below picture) of the lens (below below below) I'm using. I used my calipers :) the model of the lens needs a bit more work. I decided the hexagonal tube at the front should be 12cm wide, and then i will need a bigger box at the back of the light for power bits and stuff (the meanwell led driver is 22cm long...)





PXL_20250522_220821661 MP

# Friday 23 May - 1 hour

I finished modelling the lens thing! It was shockingly difficult to do the bit where it slopes into a triangle, especially with getting the triangles to line up with the other cylinders using constraints, it's hard to explain.



# Saturday 24 May - 4 hours

I've started modelling thge front part, the inner tube that's going to hold the lens, as is seen below.



I decided to try 3d printing the bit that the lens should in theory thread into because i want sanity and to see if i need a better way of holding the lens in than hoping it threads into the plastic. I'll have to try it again once i have petg, but i don't yet so i'm just doing in pla to see if the dimension i chose is good. The circle the lens should thread into is 0.5mm smaller than the outer diameter of the threads on the lens, so hopefully that will be good and hopefully my printer's accurate enough.



Oooo look at it go
PXL_20250524_175748476 MP



It doesn't fit :(
It almost goes on but not quite. I can almost stretch it on but it doesn't stretch. I'm thinking if i make the holder a many sided shape of some description (hexagon maybe?) and then i should have room for it to stretch (maybe??) while still holding it??? maybe???? but then I'm not sure how I'll hold the flexible bit holding the lens to the actual tube in a way that is rigid but also allows the lens holder to flex a bit...

I just thought that I could make something to clip into the weird cut out in the lens with the slanty edges, the one that took me ages to model. Still has the problem of making sure it's flexible though

Ok i think clipping into the slopey bit isn't going to be possible because it's too close to the front to have any flexibility

So uhhhh I cooked up this monstrosity :pf:


Here's how it _should_ go together with lens


Maybe it will be too thin?

Maybe it won't be flexible enough?

Maybe it will just delaminate from the layer below?

Maybe it will collapse when it's being printed? Hopefully the archedness is good enough that it won't need supports...

I don't know, but lets find out


PXL_20250524_223842524 MP

That was such a scary print to watch but IT WORKS!!!!!!!!!!!!!!!!!!!!! I am so happy

goodnight github

# Sunday 25 May - 2 hours

I edited the holder a little so the clippy bits go a little further inwards, just to give a slightly tighter fit on the lens. I also made it a teeny bit less long, because otherwise i think the front of the tube would have stopped the lens from going all the way in properly.

Here are the dimensions of the LED, I don't know if I'll directly hold it with PETG or if I'll make a wooden bit to hold it...


I really don't know how i'm going to mount the LED, it will get HOT and any normal filaments will just warp. I also don't know how I'm going to mount the cooler to it, and I also don't know how the temperature sensing is going to work. Oh and i'll probably need 12v power for the fan.... yay another power supply...

Over lunch I decided I'll probably use some 3mm mdf i have, and cut out a whole for the led and cooler to hold the led. If that makes any sense

So I pressed the button on the mouser website to get a free cad model of the led and it just worked! They did it very quickly too.

Here's a cross section of what I have now, I've started doing the outer tube and I have arms inside it to hold the wood(?) that the LED will be mounted to.


# Monday 26 May - 1 hour

So i was planning to attach the led to the mdf and the mdf to the 3d print using superglue, but uhhh apparently if superglue gets heated up it produces toxic fumes?? so maybe I'll use a 2 part epoxy of some kind of a some other sort of adhesive. from searching, apparently water based adhesives can be good for heat resistance.

I now have this platform (the grey bit) for the LED! The LED goes behind the wood because then it makes it very impossible that the LED will ever crash into the lens, which is good! And if somehow the lens does go to far back, it just hits the mdf which would be absolutely fine.



# Tuesday 27 May - 1.5 hours?

I was thinking about my LED mounting and I realised that since the LED is so bright, there's the possibility it could reflect off of the sides of the MDF hole? I don't know if that would be a problem but it's something to think about.

I was also thinking about how I'm going to move the lens, and I've pretty much decided to use a servo I think. I watched [this](https://youtu.be/MDk4SfTNr8M) video which shows how to open up a servo to get a wire out of the internal potentiometer to get feedback on what the current rotation is. So therefore i can find what rotation the user has manually moved it to, and I can store that rotation and then recall it! For storing settings, I'm thinking I'll have a bank of buttons and a SET button, like how a pipe organ stores registrations for stops. 

Also, I discovered that noctua makes fans that can run on 5V, meaning i won't need another psu!

I think I will need heatpipes to draw heat away from the LED, down the tube, and to a cooler towards the back of the light, because there is really not much space inside the tube for a cooler and fan, there's a 7.4cm gap inside which is unlikely to be enough for a big enough heatsink+fan.

I found [this](https://uk.farnell.com/amec-thermasol/mhp-2040a200a/heat-pipe-flat-200mmx40mmx2mm/dp/3972210) heat pipe but £20 seems kind of really expensive...

[This one](https://www.digikey.co.uk/en/products/detail/advanced-thermal-solutions-inc/ATS-HP-F9L200S70W-014/5049697) is from digikey and it can transport 90W of heat, so I might want two of them.  One heat pipe is £3.67. But, it's from digikey which means shipping is £12 unless i spend more than £33. So unless i decide to buy something else also from digikey, that's not going to be that helpful. I could buy the filament on digikey, but that's still not going to take the cost over £33.

Hmmm I realise i may not need nearly as beefy a cooler as i think because uhhh LEDs are supposed to be efficient.=
~~The LED I'm using doesn't explicitly say the efficiency and the heat output in the datasheet, but it does say that the typical luminous efficacy is 147lm/W, and in a worst case the minimum luminous flux is 15368lm. 15368 divided by 147 is 104.5W, meaning in a worst case the wattage~~ I just realised that lm/W is how many lumens are output for how many watts input, not whatever i thought it was.

I am quite confused with how much of the power input to an led is emitted as heat

I found [this datasheet](https://otmm.lumileds.com/adaptivemedia/6b684cddbefe74c4e4a88ed494320dc871c47925) about the LED that gives some information about its thermals, but nothing specific, but it does give things like how to measure the temperature with a thermocouple and how to mount a heatsink to it which would probably be helpful, and it mentions that you need a heatsink of enough wattage but it doesn't say anything about how to find that heatness :(

[This example](https://www.arduinolearning.com/code/max6675-and-arduino-example.php) I found shows how to use a thermocouple module with an arduino, which should be comparable to using it with the rp2040 i think. I also found [this thermocouple module](https://www.amazon.co.uk/DollaTek-MAX6675-Interface-Thermocouple-Temperature/dp/B07DK8VG87/) on amazon for £4.99. I'll also need a thermocouple wire, and they seem to be cheapest on digikey (shipping >:( ) but mouser has rather pitiful offerings for thermal things it seems which is sad: [1m wire](https://www.digikey.co.uk/en/products/detail/labfacility-ltd/XE-3529-001/25806221)  [30cm wire](https://www.digikey.co.uk/en/products/detail/labfacility-ltd/XE-0428-001/25935742)  A thermocouple works by having two dissimilar metals and when a heat is applied it makes a small voltage apparently, I don't really understand how it works but i thought i'd say something so it sounds like i have some idea about what i'm doing.

# Wednesday 28 May - 3 hours
Ok! I found [this video](https://www.youtube.com/watch?v=Lqbyu5BGthc&t=118s) which shows how to calculate the heat power output of an LED! yippee!

Now all I have to do is mentally process this scary looking equation:


I could not find a value for K in the datasheet (K is the luminous efficacy of radiation, and you need to know the radiant flux to find that, which isn't in the datasheet) so I searched how to find the heat power output of an led and apparently LEDs generally output 80% of energy input as heat, so apparently you should generally design for all of the power input to be output as heat. hhhhhhhhhhhhhhhhhhhhhhh. well anyway that was some nice research and wikipediaing, and i got to see a video of a funny looking man talk to me about LEDs for 5 minutes, many times

(that was 30 minutes)

Ok! Mouser does in fact have heat pipes! After a lot of looking and figuring out datasheets, I quite like the [ATS-HP-F7L200S65W-018](https://www.mouser.co.uk/ProductDetail/Advanced-Thermal-Solutions/ATS-HP-F7L200S65W-018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) heat pipe (catchy name, I know) [(datasheet)](https://www.mouser.co.uk/datasheet/2/596/Heat_Pipes-1480426.pdf) (The picture on mouser has multiple heat pipes with a heatsink attached but I believe it is actually just a heatpipe. It can transfer up to 61W of heat energy, so I will have 2 of them to remove up to 122W of heat which should be more than enough. Each heatpipe is 11.2mm wide and 3.5mm tall and 200mm long and costs only £3.96 yay. Two heatpipes will take up 22.4mm roughly and be £7.92. If I decide i need another heatpipe, I can get another one and it will still fit on the 38mm LED. Perhaps a 150mm long heat pipe will be enough? I'll keep designing my light and decide what length I need. For 150mm, the [ATS-HP-F5L150S40W-025](https://www.mouser.co.uk/ProductDetail/Advanced-Thermal-Solutions/ATS-HP-F5L150S40W-025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) looks good, it's 59W and £3.23, and 8mm wide.

(that was also probably 30 minutes)

[This towerpro sg90](https://www.mouser.co.uk/ProductDetail/Soldered/101246?qs=IKkN%2F947nfCky%252BicgAH2DA%3D%3D) servo motor looks good, it's on mouser meaning i can have my free shipping and it's £4.82. Apparently it needs 5V power but the logic can be run at 3v so I can use it with the rp2040 yay. The datasheet says it is both 9 grams and 14 grams though. I guess it's 14 grams including the wire? the datasheet is very little but it's common so sure. I feel like the electronics shop near me would have one?
Also totally unrelated but if you invert the phase of one channel of stereo music and then mix them down to mono, it very often filters out the voice which is nice so i can have songs i like without the singer, or often just with the backing vocals, and without actively looking for an instrumental version.

And that servo even has a 3d model already!

I found some servo I had lying around which is a knock-off SG90, so i decided I'd solder a sensor pin to it like in the video i linked
PXL_20250528_144646962 MP~2

I've been trying out the servo with my arduino uno r4 wifi, and i spent ages confused at why it was moving in such big steps. I assumed it's because it's a cheap knockoff servo, but when trying to search for why this was happening i found someone else who has an uno r4 and their stepper motor was moving in large steps. Apparently, there was a problem with uno r4s which had something to do with the PWM duty cycle, so i did an update and now it's fine! That was weird, though. Using the arduino serial plotter, I found that there is a very linear correlation between the sense pin of the servo and the angle it's rotated to, which is nice because it means i can do some code to just find a scale and offset to convert from analogue input to an angle which can be stored and sent to the servo. Yes I'm doing this to procrastinate figuring out how I'm mounting the servo in the spotlight. Below is a section of the serial plotter where the blue line is the target angle and the green line is the analogue value (which i did some manual scaling of)



I was initially trying to do a sweep of angles and then map each angle to an analogue input, but that was too complex as i think instead i can just get two points and figure it out.

Maths!

Revising for my maths GCSE next week well

I even commited the code i did to the github repo! I just added a feature that lets you set a range of motion and the servo will stop you from going further by activating when it's past the motion and moving back until it's within the range, then deactivating again.

ooo a video too

https://github.com/user-attachments/assets/37b45619-cd76-4aad-be02-627f6d1e754e

ok what why does github think it's just sound i promise it's a video if you try hard enough

I made it vaguely store position values, but it's a little sqwonky in that it keeps on thinking the pin is connected to + even when it's not, it's very odd. this means that when you press one and then press another, it will quickly flap between the two because for some time it thinks both are being pressed...

I attempted some onshaping today, but i just drew some lines so i don't think you really need to see that, it was for estimating the needed heatpipe length, and i drew the start of a sketch for mounting the servo (it's 3 lines so far)

# Thursday 29 May - 3.5 hours

Agggggh I wrote so much for today, i should really start copying out what i've written so edge can't discard the tab and get rid of everything. Normally it shows the prompt to restore what i had, but not this time i guess :(
Here's my attempt at vaguely recreating what i wrote, with trawling through my clipboard history for screenshots:

Woah look at my servo mount!



I did some more maths to figure out a probably good diameter for the cog



I watched [this somewhat vague video](https://www.youtube.com/watch?v=wLZq1ZXhPfE) to figure out how to make the pinion (straight cog thing).

I had this, first, but...

Screenshot from 2025-05-29 16-42-44

...i then realised that the pinion would really want to snap if it was printed with the rest of the inner tube, so i redesigned it to be glued onto the inner tube, meaning it can be printed flat, which will be much stronger due to the orientation of the layer lines.
And now i have this:



I may want to swap the SG90 servo for an MG90S, it's basically the same thing but with metal gears which are finer, meaning it should be quieter, stronger, and not go crunchy when you push it too much like mine does.

I also edited the code a bit to remove some weirdness with the rotation limiting, which included fixing a bug where occasionally the servo would decide to suddenly rotate all the way to the other side

Also, I shortened the length of the outer tube from whatever it was before (180 maybe?) to 155mm which is more fitting.

I just added a vent so it doesn't bake and melt itself!



From a quick search, [this cpu cooler](https://www.amazon.co.uk/Thermalright-AXP90-X53-Profile-TL-9015-Technology/dp/B0BJPWX8B5/) looks like it could be good

Oooooo how about an AIO cooler? It's got tubes so i won't have to worry about heat pipes, although i will need to get 12V... I think I might just stick to heat pipes and a heat sink in the back with a 5v fan...

AAAAAAAAAAAAAAAAAAAAAAAAAAAAAAAAAAAAAAAAAAAAAAAAA the led driver is out of stock 
Oh and I just realised: "Product available only to OEM/EMS and design business customers. Product is not shipped to consumers in the EU or the UK" D:
It's supposed to come back in stock on mouser on 14/08/2025, which would be much too late. It's also out of stock on digikey, but with the short date of 13/06/2025 to get it back in stock. hhhhhhhhhhhhhhhhhhhhhhhhhhhhhhhhhhhhhhhhhhhhhhhhhhhhhh
And the 5v psu is also business only WHY IS IT SO UNOBVIOUS???? is hack club a business? probably doesn't count...

Um so that's inconvenient

# Friday 30 May - 3 hours

Wow i really don't learn do i, i just did the same thing where i had written a bunch and then the tab got discarded...

lcsc had the 5v psu for cheaper, but with the handling cost and shipping it's not worth it so i'm just doing digikey.

[LED on digikey](https://www.digikey.co.uk/en/products/detail/lumileds/L2C5-40801825G3200/7344822) for £29.07+VAT

[LED Driver on digikey](https://www.digikey.co.uk/en/products/detail/mean-well-usa-inc/ELG-150-54B/7702975) for £37.98+VAT

[5V 10W PSU on digikey](https://www.digikey.co.uk/en/products/detail/mean-well-usa-inc/IRM-10-5/7704657) for £6.45+VAT

I found [this little 2W 5V to 12V converter](https://www.digikey.co.uk/en/products/detail/mean-well-usa-inc/SMU02L-12/7706871) for £3.89+VAT on digikey, which is much cheaper than buying a £20 noctua 5v fan, as i can just use the normal 12V fan that comes with whatever heatsink i get

I feel like i don't need to pwm the fan, it can just run at full speed. I considered not having a thermocouple, but i think it should so that it can know if it's destroying itself.

Helpfully, I found this schematic on [this datasheet](https://blog.embeddedexpert.io/?p=806) on how to use a max6675 thermocouple chip in a circuit, meaning i don't have to buy an overpriced thing, it can just integrate into my pcb!


Hmm i might use [this MAX31855KASA-T](https://www.digikey.co.uk/en/products/detail/analog-devices-inc-maxim-integrated/MAX31855KASA-T/2591213) for £7.05+VAT instead, it's basically the same thing but actually in production and at 3v. ([Datasheet](https://www.analog.com/media/en/technical-documentation/data-sheets/max31855.pdf))

I've (maybe?) finished my schematic! I used every GPIO pin, so hopefully i won't find i missed something and need another. If i do, i'll sacrifice a switch. I added a red LED to indicate stuff, like flashing when going past the movement limit, and lighting up when the led is too hot. I also included a circuit for the thermocouple, and i realised a switch would be good for the main power input.



# Saturday 31 May - 0.5 hours

I looked around my house for some components to see what i already have and won't have to buy, and i found 2 suitable(?) resistors, and a red led! I also did a bit of assigning of symbols to footprints, which included having to make some footprints myself.

# Sunday 01 June - 0.25 hours

happy pride month

i did a little more footprint making for things, namely the led driver. i also found a good looking fuse holder, and i think a 2.5A 5x20mm fuse should be good.

# Wednesday 04 June - 1.25 hours

I realised i'm fairly sure i don't need a resistor between the led driver and the LED, as it is a constant current driver so will regulate the current itself (hopefully?).

I was also looking at the thermocouple chip datasheet for no specific reason and found that the max31855 (the newer one that i switched to) suggests **not** having the negative of the thermocouple connected to ground because of something about power supply noise. There was also a revision of the datasheet that quietly adds the suggestion of "a 10nF differential capacitor to the T+/T- pins", to help reduce noise in measurements. I guess i'll do that then, no idea what differential means though.

Also apparently the wattage of the LED isn't a set maximum??? The graph below (blue line) shows that it can be as high as 250W at just under 56V. Interesting. Perhaps I should allow for more heatpipes then



I used a [funny calculator](https://www.digikey.co.uk/en/resources/conversion-calculators/conversion-calculator-pcb-trace-width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) online to figure out that my AC traces should be about 2.5mm thick for the absolute maximum of 2.5A i'm having.

I've also been finding components like resistors and capacitors. I found 2 roughly 40 ohm resistors which should be perfect for the optocoupler and red led, and I found a red led. I put matching footprints for them into the footprint assignment. I also found a [0.1uF capacitor on digikey](https://www.digikey.co.uk/en/products/detail/vishay-beyschlag-draloric-bc-components/K104K15X7RF5TL2/286538) for £0.18, as well as [this fuse holder](https://www.schurter.com/en/datasheet/typ_OGN.pdf), which i both put footprints for.

I also realised that the pin header I selected for the servo to connect to was actually tiny, thanks to my friend wanting to look at the 3d model and me realising the servo pins were tiny compared to the fan header. So i replaced it for a 2.54mm type header.

Now all that's left to do in the footprint assignment is the buttons, the connector for the thermocouple, and the holes for the led driver.

# Tuesday 10 June - 4 hours

I've been doing my PCB, I started with the AC side, and then did the lower power side. It took me a while to route it and do good placements for the footprints, but it should be done now! yay!



I've also made a spreadsheet of all the components, although i did just realise it's missing the servo and pin headers, although i can hopefully get those from my local electronics shop. OH THE OPTOISOLATOR!
Here's what i've got so far:



can't write much sorry i need to sleep

# Wednesday 11 June - 0.5 hours

I found that I can get an IEC power input thing that has a spot for a fuse! https://www.digikey.co.uk/en/products/detail/dit/DAC-13F/18681314 Meaning I can remove my internal fuse and the fuse can be user replaceable! This is also safer as it means that it is fused the moment it enters the spotlight, so the fuse will stop anything bad that could happen in the free wiring to the switch and to the board!



Oh yeah, yesterday I found it would be cheaper to buy the thermocouple amplifier and the 5v psu at lcsc, even with the added handling and shipping fees!

I just found that LCSC does iec power input things that not only have a spot for a fuse in them, but also have a switch in them! Even better!

I also added to the spreadsheet



# Saturday 14 June - 1 hour

I assigned 3d models to almost all the parts in my PCB, except the 5v to 12v converter which i unfortunately couldn't find online. Here's pictures! Oh yeah, i discovered kicad has an option to enable ray tracing which is entertaining to watch  my laptop struggle with





I also gave the board edge cuts, with rounded corners (yummy), as well as mounting holes, and a cut out to give room for the power plug.
I then imported it to onshape, although for some reason it decided to lose the colours of the components :/



# Monday 23 June - 1.5 hours

After importing the pcb to onshape and positioning it, i realised it's a bit big, so i've been working on getting it smaller in kicad. I decided to remove the traces connecting the led driver to the led, instead it will just be freewired, it's literally just two wires.



Size comparison, old in back new in front:


My LED driver still isn't back in stock, the website stock checker says shipment is due 13/06/2025 - We are actively pursuing delivery information with the supplier and will update our website as soon as possible. It's been like that for over a week so i'm emailing digikey support.

here's the email:

> Hello,
> 
> I've been waiting for the shipment of the Mean Well LED driver ELG-150-54B to arrive at digikey so I can order one for a somewhat time-sensitive project. The shipment was due on 13/06/2025 but 10 days later it is still not in stock.
> 
> Since it was due, the lead time checker on the website has said "We are actively pursuing delivery information with the supplier and will update our website as soon as possible."  so I was wondering if you have any updates on this shipment that you could share, or a good alternative? The HLG series seems to only dim to 10% and I'd rather not have to also use a relay as I am using all pins on my microcontroller already.
> 
> Thanks in advance,

They responded basically saying that the HLG-150-54B is the closest alternative. It's more expensive and doesn't dim to 0% so i won't be using it, and they probably didn't really read my email.

# Tuesday 24 June - 1 hour

I found a new LED driver!!!!!!!!
It's the [XLG-150-H-AB](https://www.digikey.co.uk/en/products/detail/mean-well-usa-inc/XLG-150-H-AB/10222586)!!! and it's cheaper! at £31.20 (incl. VAT) compared to the ELG one which is £37.94 (incl. VAT) so i save some money yippee

Apparently it should work, and it's smaller!!!

I realised the fan would be a smidge over 2W, which is the limit for my 5v-12v converter, so perhaps i will have to use a resistor

It does have an earth wire though so i will have to connect the earth to the plug input's earth, which is kind of nice because it felt a little weird having an earthed plug but no actual earthing in the light.

I have been considering how i'm going to have the heatsink. 
Here's a drawing (terrible, i know)



Basically, I'll have a cutout below the heatsink so it can exhaust the hot air, without just exhausting all the heat from the led inside the light. The fan will also extract ambient heat from the electronics too!

That heatsink is £20 on facebook marketplace, hopefully it's still in stock by the time i actually buy it.

I realised it's kind of impossible to solder to a heat pipe because uhh it moves heat? so instead i'll have to use thermal epoxy WHY IS THERMAL EPOXY SO EXPENSIVE WHAT

ok i found ec360 thermal glue for £6 on amazon it's not that bad

# Friday 4 July - 1 hour

I moved the microcontroller so it's more central on the board and further contemplated by heatsink choice. After consulting my friend ([Max W](https://github.com/max-worboys)), he found the cooler master 212 evo on facebook marketplace for £10, which is half the price of the low profile cooler i was looking at before. Yes, it's not low profile, but i don't think that matters all that much if it gives me more cooling headroom, is cheaper, and is more easy for other people to find (it's around £15 on ebay and pretty common, so others will be able to reproduce my project).



aaaand, as the fan on the hyper 212 evo is 2.26W (over the 2w rating of my 5v-12v boost converter), i have (with much pain) found the [SPU03L-12](https://www.digikey.co.uk/en/products/detail/mean-well-usa-inc/SPU03L-12/7707058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) which is £4.51 on digikey and is not available on LCSC, so it's more than the £3.54 i was paying for the 2w converter but this one actually provides enough power so i think it's worth it, and the cheaper cooler offsets the cost.

i really need a good good proper think about how i'm mounting and orienting the cooler. Now that i've proerly decided on a specific cooler, i can start doing it without fear of it changing because that just is the cooler i'm getting no matter what. 

goodnight github

# Saturdat 5 July - 0.5 hours

I replaced the old voltage converter on the schematic and pcb, and i have found a 3d model of the heatsink and imported it to onshape!

ALSO, i managed to find a thermocouple on LCSC!!!! for $4.56 !!!!!!!!!!!!!!!!!!!! that's a lot less than the thermocouple i had before ($7.54 less!), although it doesn't have much data available about it. It is the [ETA-G-K-24-200cm](https://lcsc.com/product-detail/Electronic-testing-accessories_ETA-ETA-G-K-24-200cm_C5144202.html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) which is 200cm but i can just coil it up inside [(manufacturer website)](https://en.tw-eta.com/index.php?c=show&id=320)

# Sunday 6 July - 2 hours

I positioned the parts how i think they will fit nicely, and i imported a model of the led driver. There was no model available for the power input part, so i modelled the important aspects in onshape which took way too long, and i made a raised bit that comes out of the light for the part to sit on so that the prongs aren't at risk of touching the heatsink (bad). and it's looking pretty good! oh also i think i have finalised my parts list. Also, I added a fan to the model.



(ignore the wires sticking out, those are from the led driver and i haven't done anything about them yet)





(yes i realise that fan needs to be the other way around, that's a future me task)

# Friday 18 July - 4 hours

SO it's been a while but i've been working on it over the past few days and i've modelled the heatpipes and i researched bending tools for heat pipes. i found a few, but the best i found was [this one](https://www.reddit.com/r/functionalprint/comments/y1ksua/pipe_bender_for_heat_pipes/). It's simple, 3d printed, and doesn't kink the heat pipe. AND, the person gave an onshape link so i could see how they modelled it! 

Heat pipes:



I had to make 2 different benders because it wasn't possible to combine all the bends into one. And the first bender has to be in 2 separate pieces that go together, or else it would be impossible to take the heat pipe out once it has been bended :pf:

Bender 1 part 1 with complete heatpipe for reference


Bender 1 part 2


Bender 1 together with complete heatpipe for reference


Bender 2 with complete heatpipe


# Sundary 20 July - 1.5 hours

guten abend

I have made the top of the electronics box separate from the main thing, AND i decided how i'm going to be mounting things!

So i'm going to be using m4 screws with nuts, it's easier than threaded inserts and both the IEC power input and the led driver and now my PCB have 4.5mm holes for m4 screws.

I have made holes for:

- the led driver!
- the electronics box roof!
- the power input!

It looks like this:



# Monday 21 July - 2 hours

I have sort of hollowed out the back of the light tube, it used to look like the first picture but now looks like the second! I also added an extra bit that sticks out slightly to give some room for the LED driver wires, and i continued adding screw holes and nut holes around

Hollowing out the back was shockingly difficult, i tried offsetting the faces and thickning them as a cut, but it would just go wonky so i ended up having to manually make a plane in exactly the right place and draw a little triangle which i cut out of the body for each side :pf: it's hard to explain

I'm just about to add extra screw holes at the top where the front and back attach but i'm going to sleep

I'm feeling like it's close to finished, although i still do need to figure out a mount for the heatsink and make a back plate the pcb attaches to, but that shouldn't be too hard right? right?????







# Tuesday 22 July - 2.5 hours

I've done the top of the attachment between the front and back!



Next up: heatsink mounting

I've just been seeing how PLA handles being pushed against my cpu heatsink when i'm running a stress test (CPU at 150-180W) and it was absolutely fine, didn't go melty at all, so PETG should be great to hold the heatsink without needing a buffer material (MDF)

Snazzy hole:



I really really hope this model of the cooler is accurate

I just finished making 2 mounting brackets to (hopefully) hold the cooler in place, they should fit inbetween the fan and heatsink, maybe they'll be noisy but oh well. I also made the base of the box nicely fit to the heatsink!



My dad just reminded me i need a mount for the light... I think i'll do that now. I'm thinking M10 bolts? (I'll need to check dimensions once i've bought the bolts and before printing)

Hey look it's a mount nub! I also put 2 little tabs on one of the sides that can be folded over the bolt because otherwise it could fall in



# Wednesday 23 July - 4 hours

I've made a nice back panel, added a silkscreen warning symbol to the part of the PCB where AC is, made a cutout to plug in a usb c cable, changed the nubs for the legs slightly, and added more fan intake holes on the front tube.



I'm thinking i'll cut the legs out of plywood, i don't think 3d printed legs would be great to hold the whole lamp with.

I just made a handle to move the front tube. 
I suddenly thought i could use one of the buttons on the back, or a key combo, to switch the fader from changing the led brightness to moving the lens, i think that would be fun.



Oh did I mention that when i did my school desk lamp project it had a really not great way of mounting the bolts to the body, it was just a superglued on thing that went over the bolt to attach it to the body, very bad and i doubt it would hold for such a bigger scale version.

LEGS!



KNOB!!





wow very productive day

# Thursday 24 July - 1 hour

I've been getting my project towards ready for submission, and i also added two more screw holes for attaching the back plate.

I gimped a wiring diagram!



I also did a better readme

Here's my ticklist so far!



I am going to do the code tomorrow, i have no doubt it won't be perfect but it should be enough to function

I have an excel spreadsheet of my BoM, but i'm too tired right now to add it to my repo as a csv and in my readme as a table so goodnight!

I am debating with myself whether or not this is a 6 or 10 point project, i guess i'll ask in one of the highway channels

# Friday 25 July - 2 hours

I did code, assigning pins to the right ones for the xiao, and i changed the pin input types from pulldown to pullup and it fixed so much quirkyness! Before i did that, touching some pins on the arduino with a finger made the servo freak out and the buttons were weird, now it's fine!! I also added the thermocouple library, but code is not yet finished. (see https://github.com/Zanduino/MAX31855/blob/master/examples/Demo/Demo.ino)

i also exported everything as step files, finalised the BoM, figured out i'm going to split the cost of filament with a friend so i can get 1kg for £8.75, and made production files.

oh and i added to the readme, asked acon if it's a 6 or 10 point project (they said 6 but maybe with extra points), and did some other things to get it good too.

# Tuesday 19 July - 1 hour

I did the code!!! yay!! I can submit now!!

# Friday 15 August - 1.5 hours

I've been ordering parts and my digikey thing arrived! I chose a cheaper but similar specs LED which was £21 compared to £34 of the original led. I've added chamfers to all the screw holes on the spotlight so that the countersunk screws i'm getting can actually countersink into the body of the light, and i also added more fan vents! I figured it would be better to have too much vent and then cover up if needed than to have too little.



# Thursday 21 August - 2 hours

My parts have arrived! I haven't got my 3d printed bits from my friend yet, and i also haven't got the screws or thermal adhesive yet, but i've got enough to do most of the soldering! 
Problems:
- The holes for the AC bits (led driver input and power input) are a smidge too small
- The footprint for the 5v to 12v dc converter is the wrong way around, but thankfully there is just about enough space on the board that it can still go on!

Soldering the surface mount components (thermocouple amplifier and a capacitor) went surprisingly smoothly!

The 5v to 12v converter works good! 

I flashed the code to the xiao, i did have to change some things because the compiler wasn't happy. But the thermocouple wasn't doing anything. So i dug around for ages and decided in the end to switch to the adafruit max31855 library which also didn't work at first, and i was seriously starting to worry i'd managed to kill it, i even started adding extra solder to the pins. Then i looked at the code (i was trying the adafruit demo) and realised i hadn't changed the default pins. And then it worked perfect!! I still have to change the real code to use the adafruit library though.

The dimensions of the heatsink are a little different to the 3d model, it's like the fins are shifted down by one fin. so i'm changing that and fixing the mounting for it.

# Friday 22 August - 1 hour

I edited the dimensions of heatsink mounting stuff in the model, i won't show a picture because there's visually not much difference but i promise it has been changed. I want to make a grating across the big hole for the heatsink but i'm going to bed so bye

# Sunday 28 September - 3 hours

Over the past month, I have:

broken the servo (chipped a gear tooth) and ordered new ones. The new ones are a bit stiffer to turn and have a physical limit on how far the spinny bit can spin, and they're a little taller

improved the servo mount!



soldered the pcb!

PXL_20250928_154606048 MP

added a screw hole to the front handle 


and otherwise finished and prepared the 3d model to be printed by my friend

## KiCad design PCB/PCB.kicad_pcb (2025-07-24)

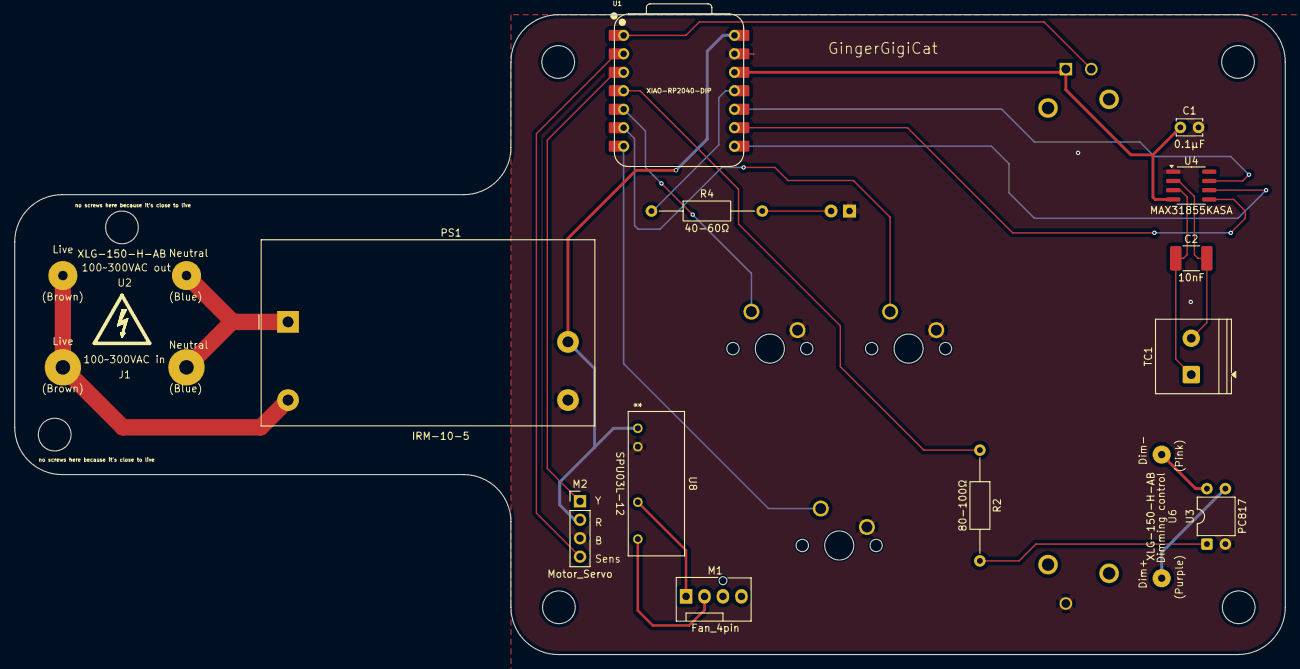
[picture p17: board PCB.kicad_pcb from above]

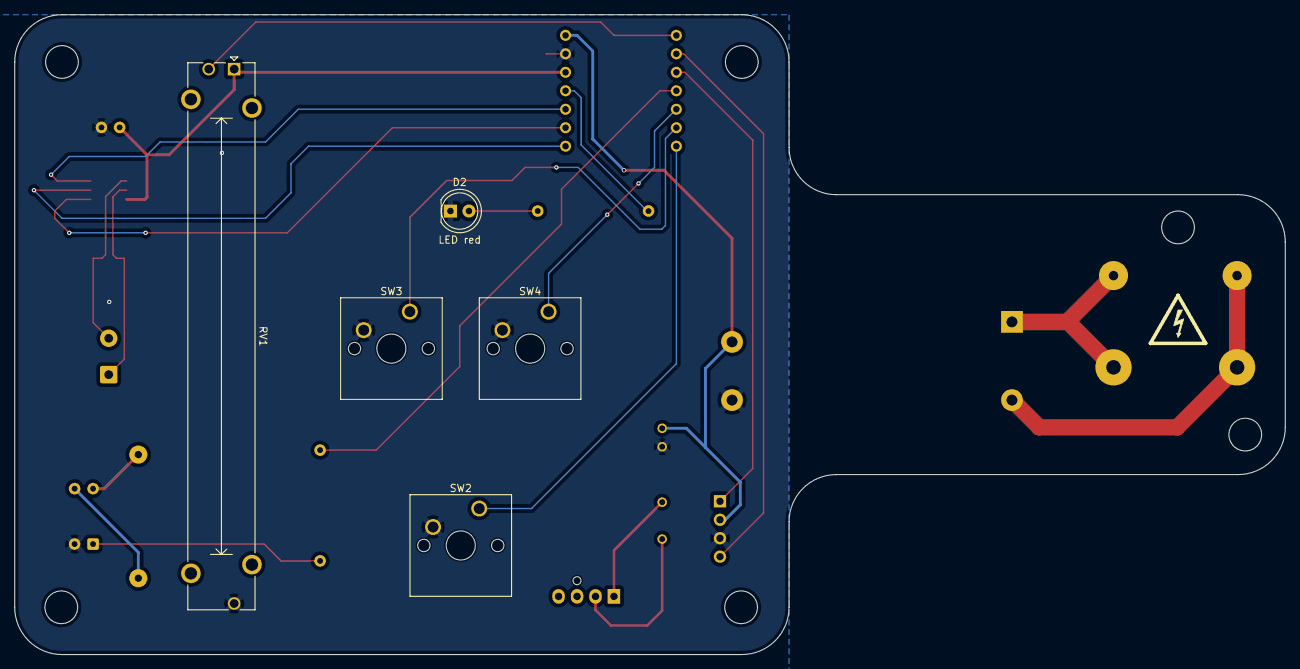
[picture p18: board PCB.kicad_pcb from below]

Board: 2 copper layers, 174.8 x 88.0 mm, 20 parts (5 on the bottom side), 24 nets.

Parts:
C1: 0.1µF; C_Disc_D3.4mm_W2.1mm_P2.50mm
C2: 10nF; C_1812_4532Metric_Pad1.57x3.40mm_HandSolder
D2: LED red; LED_D5.0mm
J1: IEC_C14_Receptacle; C14 Power input
M1: Fan_4pin; FanPinHeader_1x04_P2.54mm_Vertical
M2: Motor_Servo; PinHeader_1x04_P2.54mm_Vertical
PS1: IRM-10-5; Converter_ACDC_MeanWell_IRM-10-xx_THT
R2: 80-100Ω; R_Axial_DIN0207_L6.3mm_D2.5mm_P15.24mm_Horizontal
R4: 40-60Ω; R_Axial_DIN0207_L6.3mm_D2.5mm_P15.24mm_Horizontal
RV1: Pot; Potentiometer_Bourns_PTA6043_Single_Slide
SW2: SW_Push SET; SW_Cherry_MX_1.00u_PCB
SW3: SW_Push Pos1; SW_Cherry_MX_1.00u_PCB
SW4: SW_Push Pos2; SW_Cherry_MX_1.00u_PCB
TC1: Thermocouple_Block; TerminalBlock_Philmore_TB132_1x02_P5.00mm_Horizontal
U1: XIAO-RP2040-DIP
U2: XLG-150-H-AB; Meanwell ELG-150-54B AC side
U3: PC817; DIP-4_W7.62mm
U4: MAX31855KASA; SOIC-8_3.9x4.9mm_P1.27mm
U6: Meanwell ELG-150-54B dim pins; Meanwell ELG-150-54B Other Side
U8: SPU03L-12; SPU03L-12_MWU

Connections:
+3V3: C1.1, RV1.1, U1.12 (3V3), U4.4 (V_{CC})
+5V: M2.2 (+), PS1.4 (+Vo), U1.14 (VBUS), U8.1 (VIN+)
GND: C1.2, D2.1 (K), M2.3 (-), PS1.3 (-Vo), RV1.3, SW2.2, SW3.2, SW4.2, U1.13 (GND), U3.2, U4.1 (GND), U8.2 (VIN-)
unnamed: D2.2 (A), R4.2
unnamed: J1.1 (L), PS1.2 (AC/L), U2.1 (L_in)
unnamed: J1.2 (N), PS1.1 (AC/N), U2.2 (N_in)
unnamed: M1.2 (+), U8.7 (VOUT+)
unnamed: M1.1 (-), U8.5 (VOUT-)
unnamed: M2.1 (PWM), U1.3 (GPIO28/ADC2/A2)
unnamed: M2.4 (Sense), U1.2 (GPIO27/ADC1/A1)
unnamed: R2.2, U3.1
unnamed: C2.1, TC1.1 (+), U4.3 (T+)
unnamed: C2.2, TC1.2 (-), U4.2 (T-)
unnamed: SW2.1, U1.7 (GPIO0/TX)
unnamed: U1.8 (GPIO1/RX), U4.6 (~CS)
unnamed: U1.9 (GPIO2/SCK), U4.5 (SCK)
unnamed: R4.1, U1.11 (GPIO3/MOSI)
unnamed: U1.10 (GPIO4/MISO), U4.7 (SO)
unnamed: SW4.1, U1.5 (GPIO6/SDA)
unnamed: SW3.1, U1.6 (GPIO7/SCL)
unnamed: RV1.2, U1.1 (GPIO26/ADC0/A0)
unnamed: R2.1, U1.4 (GPIO29/ADC3/A3)
unnamed: U3.3, U6.1 (Dim+)
unnamed: U3.4, U6.2 (Dim-)

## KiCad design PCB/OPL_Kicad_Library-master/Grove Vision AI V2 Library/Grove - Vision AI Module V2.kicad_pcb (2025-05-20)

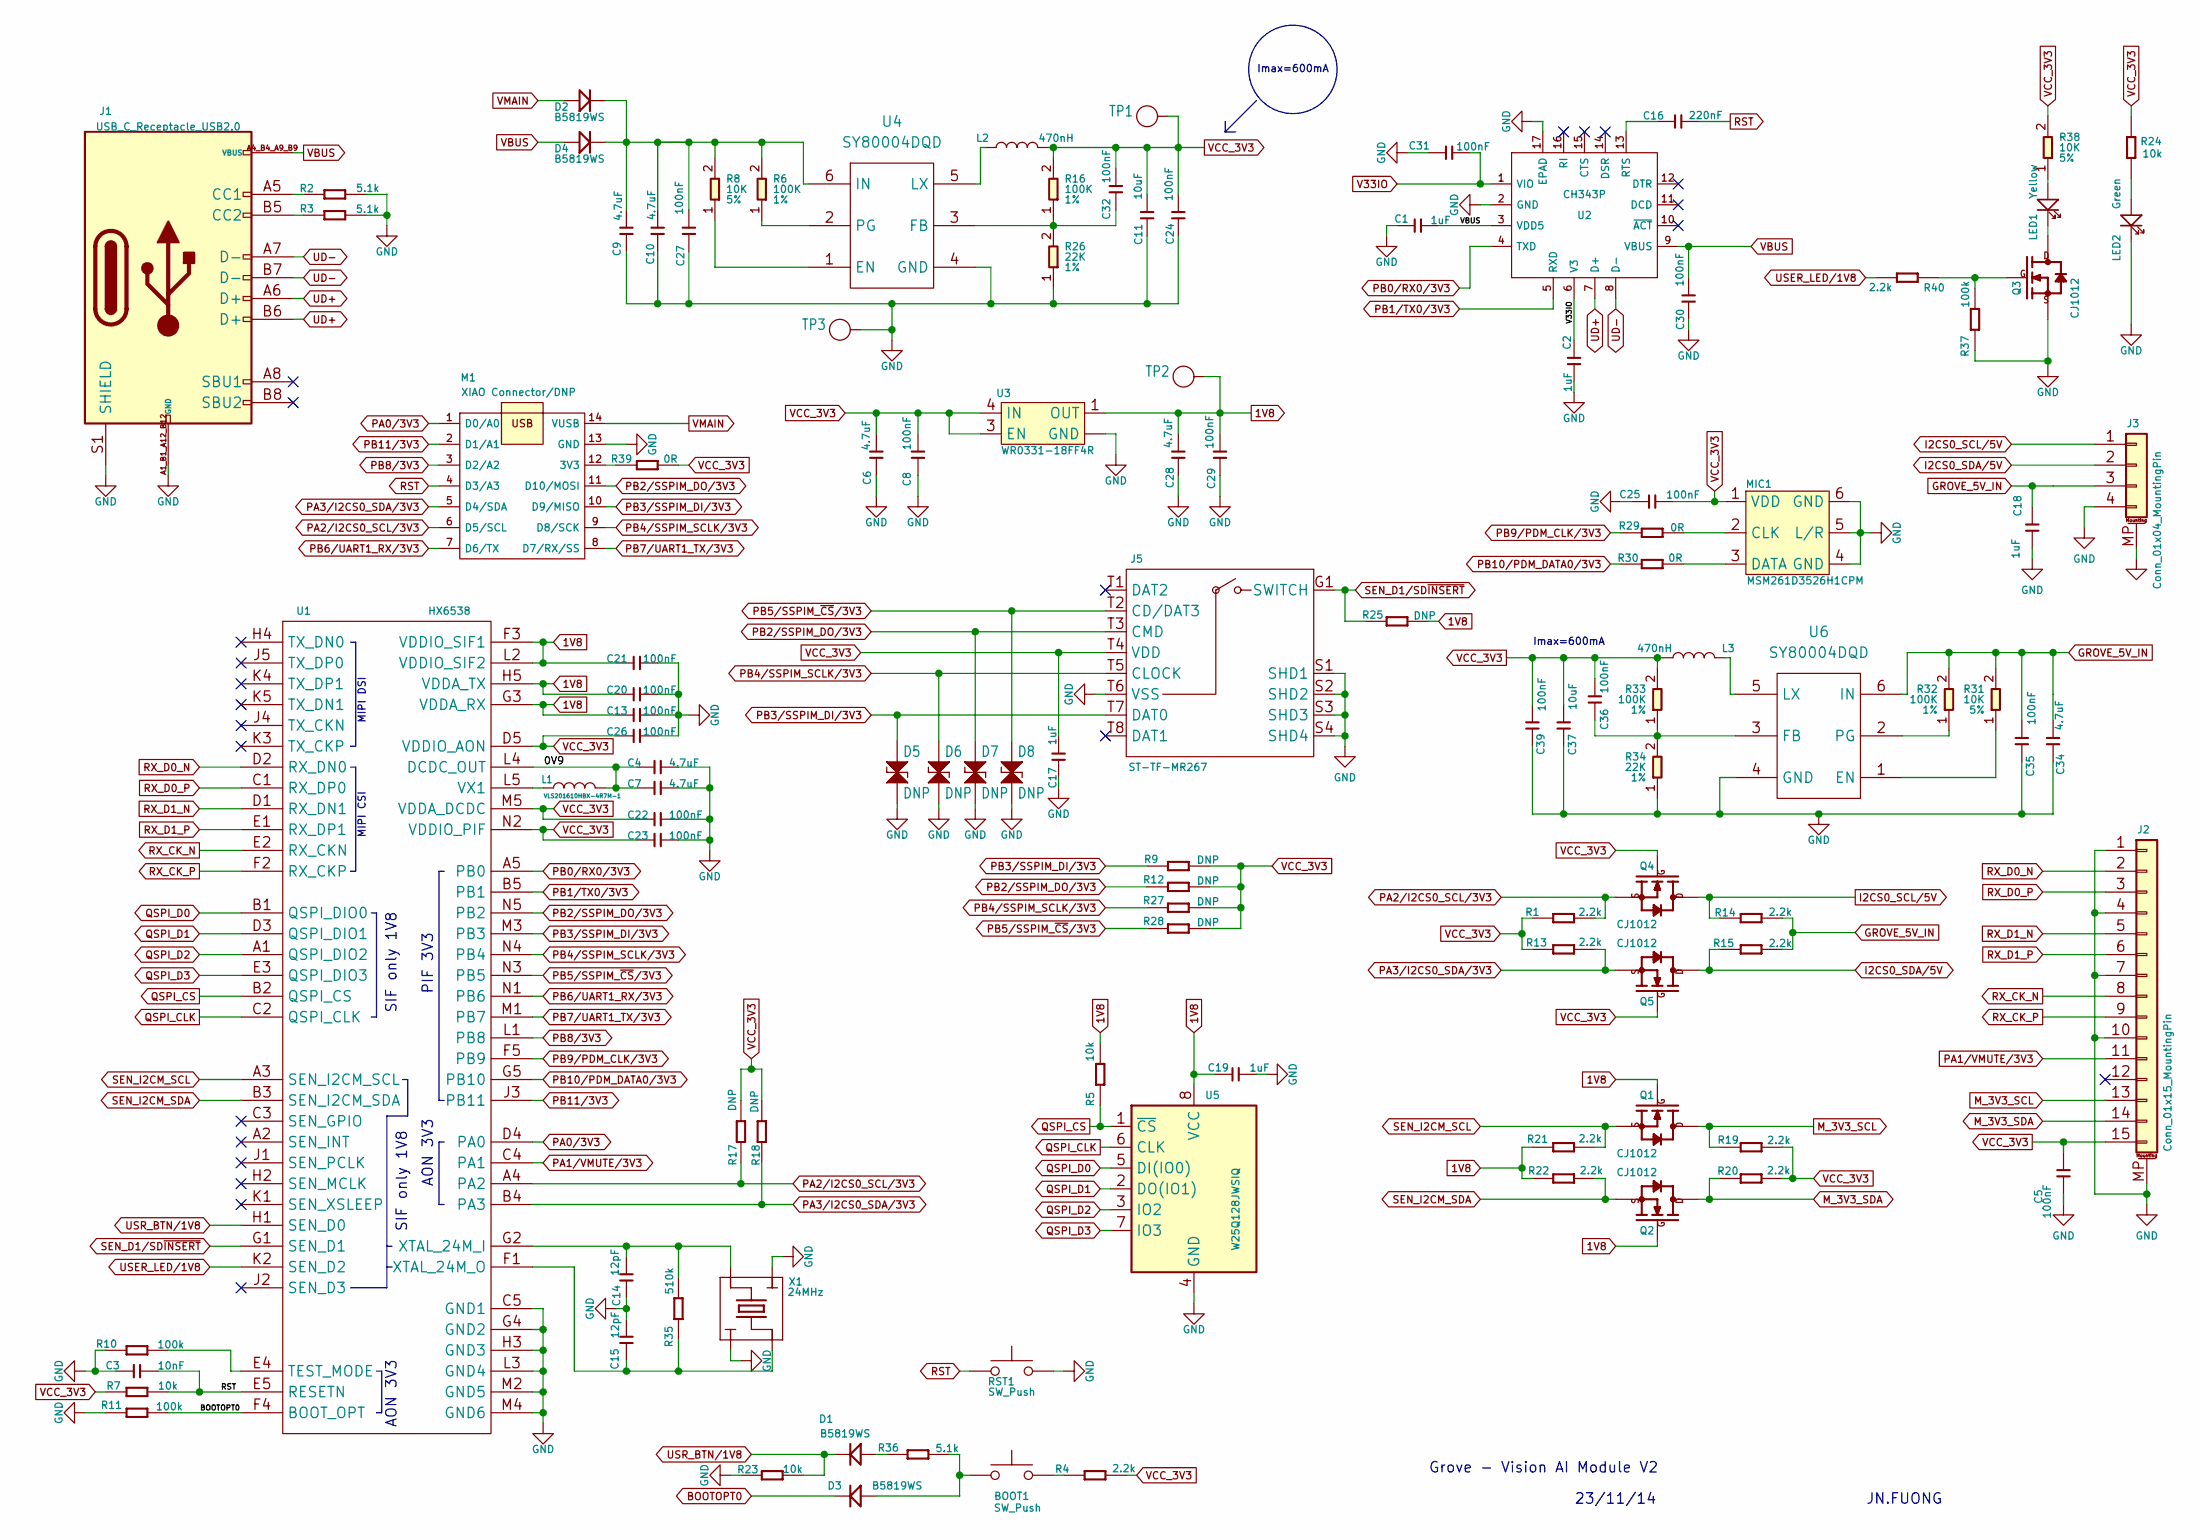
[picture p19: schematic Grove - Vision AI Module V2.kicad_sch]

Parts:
BOOT1: SW_Push; SW_Push_1P1T_NO_Vertical_Wuerth_434133025816
C1, C2, C17, C18, C19: 1uF; C0402
C3: 10nF; C0402
C4, C6, C7, C9, C10, C28, C34: 4.7uF; C0402
C5, C8, C13, C20, C21, C22, C23, C24, C25, C26, C27, C29, C30, C31, C32, C35, C36, C39: 100nF; C0402
C11, C37: 10uF; C0402
C14, C15: 12pF; C0402
C16: 220nF; C0402
D1, D2, D3, D4: B5819WS; D0805_SOD323
D5, D6, D7, D8: DNP; R0402; MPN DF2S6.8FS
J1: USB_C_Receptacle_USB2.0; USB2.0-TYPE-C
J2: Conn_01x15_MountingPin; FPC_DNC_15P_1.0mm
J3: Conn_01x04_MountingPin; 4P-SMD-2.0mm-RIGHT
J5: ST-TF-MR267; SD-TF-MR267; MPN SD-TF-MR267
L1: VLS201610HBX-4R7M-1; L0806
L2, L3: 470nH; L0603
LED1: Yellow; LED0402
LED2: Green; LED0402
M1: XIAO Connector/DNP; XIAO_Socket
MIC1: MSM261D3526H1CPM; MIC6P-3.5X2.65X0.94MM
Q1, Q2, Q3, Q4, Q5: CJ1012; SOT523
R1, R4, R13, R14, R15, R19, R20, R21, R22, R40: 2.2k; R0402
R2, R3, R36: 5.1k; R0402
R5, R7, R23, R24: 10k; R0402
R6, R16, R32, R33: 100K; R0402; Power Rating 1%; MPN RC0402JR-074K7L
R8, R31, R38: 10K; R0402; Power Rating 5%; MPN RC0402JR-074K7L
R9, R12, R17, R18, R25, R27, R28: DNP; R0402
R10, R11, R37: 100k; R0402
R26, R34: 22K; R0402; Power Rating 1%; MPN RC0402JR-074K7L
R29, R30, R39: 0R; R0402
R35: 510k; R0402
RST1: SW_Push; SW_Push_1P1T_NO_Vertical_Wuerth_434133025816
TP1, TP2, TP3: Test Point; TP-D35MIL; Part Type Test Point
U1: HX6538; WLCSP65_5.6x2.3x0.56mm
U2: CH343P; QFN-16-EP_3x3mm_P0.5mm_EP1x1mm
U3: WR0331-18FF4R; X2SON-4
U4, U6: SY80004DQD; DFN6-0.5-1.5X1.5X0.65MM; MPN SY80004DQD
U5: W25Q128JWSIQ; SOIC-8_5.23x5.23mm_P1.27mm
X1: 24MHz; 4P2016

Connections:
1V8: C13.1, C19.2, C20.1, C21.1, C28.1, C29.2, Q1.1 (G), Q2.1 (G), R5.1, R21.2, R22.2, R25.1, TP2.1 (T), U1.F3 (VDDIO_SIF1), U1.G3 (VDDA_RX), U1.H5 (VDDA_TX), U1.L2 (VDDIO_SIF2), U3.1 (OUT), U5.8 (VCC)
/0V9: C4.1, C7.1, L1.2, U1.L4 (DCDC_OUT)
BOOTOPT0: D3.1 (K), R11.1, U1.F4 (BOOT_OPT)
GND: C1.2, C2.2, C3.2, C4.2, C5.2, C6.2, C7.2, C8.1, C9.2, C10.2, C11.1, C13.2, C14.2, C15.1, C17.2, C18.2, C19.1, C20.2, C21.2, C22.2, C23.2, C24.1, C25.1, C26.2, C27.1, C28.2, C29.1, C30.1, C31.2, C34.2, C35.1, C37.1, C39.1, D5.1, D6.1, D7.1, D8.1, J1.A1_B1_A12_B12 (GND), J1.S1 (SHIELD), J2.1, J2.4, J2.7, J2.10, J2.MP (MountPin), J3.4, J3.MP (MountPin), J5.S1 (SHD1), J5.S2 (SHD2), J5.S3 (SHD3), J5.S4 (SHD4), J5.T6 (VSS), LED2.1 (K), M1.13 (GND), MIC1.4 (GND), MIC1.5 (L/R), MIC1.6 (GND), Q3.2 (S), R2.2, R3.2, R10.2, R11.2, R23.2, R26.1, R34.1, R37.2, RST1.2, TP3.1 (T), U1.C5 (GND1), U1.G4 (GND2), U1.H3 (GND3), U1.L3 (GND4), U1.M2 (GND5), U1.M4 (GND6), U2.2 (GND), U2.17 (EPAD), U3.2 (GND), U3.T (GND), U4.4 (GND), U5.4 (GND), U6.4 (GND), X1.2 (1), X1.4 (3)
GROVE_5V_IN: C18.1, C34.1, C35.2, J3.3, R14.1, R15.1, R31.2, R32.2, U6.6 (IN)
I2CS0_SCL/5V: J3.1, Q4.3 (D), R14.2
I2CS0_SDA/5V: J3.2, Q5.3 (D), R15.2
M_3V3_SCL: J2.13, Q1.3 (D), R19.2
M_3V3_SDA: J2.14, Q2.3 (D), R20.2
unnamed: BOOT1.2, R4.2
unnamed: D1.2 (A), R36.2
unnamed: C9.1, C10.1, C27.2, D2.1 (K), D4.1 (K), R6.2, R8.2, U4.6 (IN)
unnamed: BOOT1.1, D3.2 (A), R36.1
unnamed: J1.A5 (CC1), R2.1
unnamed: J1.B5 (CC2), R3.1
unnamed: LED1.2 (A), R38.1
unnamed: LED1.1 (K), Q3.3 (D)
unnamed: LED2.2 (A), R24.2
unnamed: M1.12 (3V3), R39.2
unnamed: MIC1.2 (CLK), R29.1
unnamed: MIC1.3 (DATA), R30.1
unnamed: Q3.1 (G), R37.1, R40.2
unnamed: R10.1, U1.E4 (TEST_MODE)
unnamed: L1.1, U1.L5 (VX1)
unnamed: C14.1, R35.1, U1.G2 (XTAL_24M_I), X1.3 (4)
unnamed: C15.2, R35.2, U1.F1 (XTAL_24M_O), X1.1 (2)
unnamed: C16.2, U2.13 (RTS)
unnamed: R8.1, U4.1 (EN)
unnamed: C32.1, R16.1, R26.2, U4.3 (FB)
unnamed: L2.1, U4.5 (LX)
unnamed: R6.1, U4.2 (PG)
unnamed: R31.1, U6.1 (EN)
unnamed: C36.1, R33.1, R34.2, U6.3 (FB)
unnamed: L3.1, U6.5 (LX)
unnamed: R32.1, U6.2 (PG)
PA0/3V3: M1.1 (D0/A0), U1.D4 (PA0)
PA1/VMUTE/3V3: J2.11, U1.C4 (PA1)
PA2/I2CS0_SCL/3V3: M1.6 (D5/SCL), Q4.2 (S), R1.1, R17.2, U1.A4 (PA2)
PA3/I2CS0_SDA/3V3: M1.5 (D4/SDA), Q5.2 (S), R13.1, R18.2, U1.B4 (PA3)
PB0/RX0/3V3: U1.A5 (PB0), U2.4 (TXD)
PB1/TX0/3V3: U1.B5 (PB1), U2.5 (RXD)
PB2/SSPIM_DO/3V3: D7.2, J5.T3 (CMD), M1.11 (D10/MOSI), R12.2, U1.N5 (PB2)
PB3/SSPIM_DI/3V3: D5.2, J5.T7 (DAT0), M1.10 (D9/MISO), R9.2, U1.M3 (PB3)
PB4/SSPIM_SCLK/3V3: D6.2, J5.T5 (CLOCK), M1.9 (D8/SCK), R27.2, U1.N4 (PB4)
PB5/SSPIM_~CS/3V3: D8.2, J5.T2 (CD/DAT3), R28.2, U1.N3 (PB5)
PB6/UART1_RX/3V3: M1.7 (D6/TX), U1.N1 (PB6)
PB7/UART1_TX/3V3: M1.8 (D7/RX/SS), U1.M1 (PB7)
PB8/3V3: M1.3 (D2/A2), U1.L1 (PB8)
PB9/PDM_CLK/3V3: R29.2, U1.F5 (PB9)
PB10/PDM_DATA0/3V3: R30.2, U1.G5 (PB10)
PB11/3V3: M1.2 (D1/A1), U1.J3 (PB11)
QSPI_CLK: U1.C2 (QSPI_CLK), U5.6 (CLK)
QSPI_CS: R5.2, U1.B2 (QSPI_CS), U5.1 (~CS)
QSPI_D0: U1.B1 (QSPI_DIO0), U5.5 (DI(IO0))
QSPI_D1: U1.D3 (QSPI_DIO1), U5.2 (DO(IO1))
QSPI_D2: U1.A1 (QSPI_DIO2), U5.3 (IO2)
QSPI_D3: U1.E3 (QSPI_DIO3), U5.7 (IO3)
RST: C3.1, C16.1, M1.4 (D3/A3), R7.1, RST1.1, U1.E5 (RESETN)
RX_CK_N: J2.8, U1.E2 (RX_CKN)
RX_CK_P: J2.9, U1.F2 (RX_CKP)
RX_D0_N: J2.2, U1.D2 (RX_DN0)
RX_D0_P: J2.3, U1.C1 (RX_DP0)
RX_D1_N: J2.5, U1.D1 (RX_DN1)
RX_D1_P: J2.6, U1.E1 (RX_DP1)
SEN_D1/SD~INSERT: J5.G1 (SWITCH), R25.2, U1.G1 (SEN_D1)
SEN_I2CM_SCL: Q1.2 (S), R21.1, U1.A3 (SEN_I2CM_SCL)
SEN_I2CM_SDA: Q2.2 (S), R22.1, U1.B3 (SEN_I2CM_SDA)
UD+: J1.A6 (D+), J1.B6 (D+), U2.7 (D+)
UD-: J1.A7 (D-), J1.B7 (D-), U2.8 (D-)
USER_LED/1V8: R40.1, U1.K2 (SEN_D2)
USR_BTN/1V8: D1.1 (K), R23.1, U1.H1 (SEN_D0)
V33IO: C2.1, C31.1, U2.1 (VIO), U2.6 (V3)
VBUS: C1.1, C30.2, D4.2 (A), J1.A4_B4_A9_B9 (VBUS), U2.3 (VDD5), U2.9 (VBUS)
VCC_3V3: C5.1, C6.1, C8.2, C11.2, C17.1, C22.1, C23.1, C24.2, C25.2, C26.1, C32.2, C36.2, C37.2, C39.2, J2.15, J5.T4 (VDD), L2.2, L3.2, MIC1.1 (VDD), Q4.1 (G), Q5.1 (G), R1.2, R4.1, R7.2, R9.1, R12.1, R13.2, R16.2, R17.1, R18.1, R19.1, R20.1, R24.1, R27.1, R28.1, R33.2, R38.2, R39.1, TP1.1 (T), U1.D5 (VDDIO_AON), U1.M5 (VDDA_DCDC), U1.N2 (VDDIO_PIF), U3.3 (EN), U3.4 (IN)
VMAIN: D2.2 (A), M1.14 (VUSB)

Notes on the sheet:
MIPI CSI
AON 3V3
MIPI DSI
PIF 3V3
SIF only 1V8
Imax=600mA
23/11/14
Grove - Vision AI Module V2
JN.FUONG

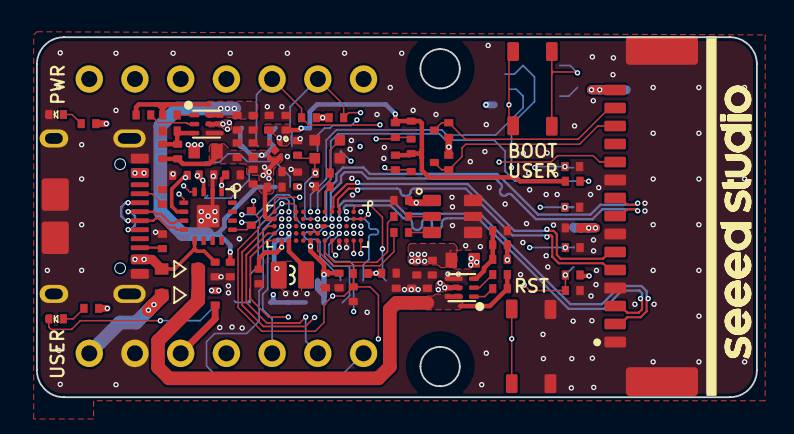
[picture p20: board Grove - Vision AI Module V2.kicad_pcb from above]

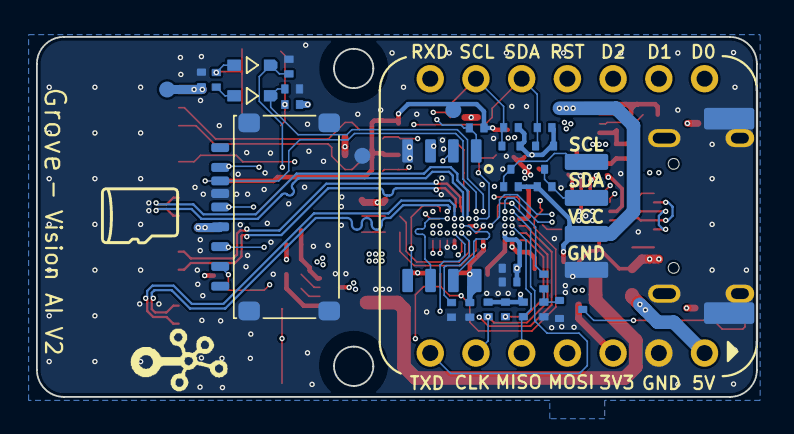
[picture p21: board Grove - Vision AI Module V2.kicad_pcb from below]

Board: 4 copper layers, 40.0 x 20.0 mm, 112 parts (31 on the bottom side), 75 nets.

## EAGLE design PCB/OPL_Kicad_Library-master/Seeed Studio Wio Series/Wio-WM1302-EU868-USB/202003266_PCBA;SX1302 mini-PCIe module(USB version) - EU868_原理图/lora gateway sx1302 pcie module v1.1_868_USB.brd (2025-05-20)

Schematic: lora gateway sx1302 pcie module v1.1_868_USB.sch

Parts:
ANT1: U.FL-R-SMT-1(10); U-FL3P-SMD-2.6X2.6X1.0MM
ANT2: DNP; U-FL3P-SMD-2.6X2.6X1.0MM
C1, C12, C15, C19, C23, C25, C26, C29, C32, C41, C43, C45, C65, C67, C80, C83, C86, C88: 100nF; C0402
C2, C75: 2.2pF; C0402
C3, C92: 10uF; C0603
C4, C8, C11, C16, C17, C18, C64: 56pF; C0402
C5, C6, C9, C10: 3.6pF; C0402
C7, C91: 5.6pF; C0402
C13, C20, C21, C24, C28, C35, C39, C40, C42, C44, C47, C48, C76, C87, C89: 1uF; C0402
C14, C38, C57, C66, C81, C84: 10pF; C0402
C22, C27, C33: 10uF; C0603@1
C30, C56, C74, C77, C78, C79: DNP; C0402
C31: DNP; C0603@1
C34, C46, C63: 470nF; C0402
C36: 47nF; C0402
C37: 47pF; C0402
C49: 4.7uF; C0603
C50, C62, C85: 10nF; C0402
C51: 1nF; C0402
C52, C55: 100pF; C0402
C53, C60, C61: 3.3pF; C0402
C54: 39pF; C0402
C58: 1.3pF; C0402
C59, C68, C73: 1.8pF; C0402
C69, C70, C71, C72: 10uF; C0805
C82: 2.7pF; C0402
C90: 2.2uF; C0603
D1, D4: Green; LED-0402
D2: Red; LED-0402
D3: Blue; LED-0402
D5: LXES15AAA1-153; ESD-0402
D6: DNP; ESD-0402
D7: BAT54XV2T1G; SOD-523
FB1: BLM15PD121SN1D; F0402
J1: DNP; PCIE52P-0.8-50.95X30MM
L1: LQP15MN1N2B02D; L0402
L2: LQW15AN6N8G00D; L0402
L4: 0R; F0603
L5: LQH44PN1R0NP0L; L4.4X3.0MM
L6, L14, L20: MLZ2012M150WT; L0805
L7, L15, L18, L21: DNP; L0402
L8: LQW15AN3N0B00; L0402
L9: LQW15AN47NJ00D; L0402
L10: LQW15AN2N5B00D; L0402
L11: LQW15AN4N7C00D; L0402
L12, L13: LQW15AN12NG00D; L0402
L16: LQW15AN7N5G00D; L0402
L17, L24: LQW15AN5N6C10D; L0402
L22: LQW15AN15NG00D; L0402
Q8: CJ2101; SOT-323
Q10: CJ2102; SOT-323
R1, R4, R33, R34, R38, R42, R57, R65, R71: 10k; R0402
R2, R7: 0R; R0603
R3, R8, R11, R12, R43, R44, R46, R49, R51, R55, R56, R59, R60, R61, R62, R63, R67, R70, R72, R73, R74, R75, R76, R81: DNP; R0402
R5, R10, R14, R15, R16, R39, R40, R41: 100R; R0402
R6, R9, R37: 220R; R0402
R13, R35, R52: DNP; R0603
R17, R18, R19, R20, R21, R22, R23, R24, R25, R26, R27, R28, R29, R36, R45, R48, R50, R53, R54, R69, R77: 0R; R0402
R30, R31, R32: 680R; R0402
R47, R79: 1k; R0402
R58, R68: 4.7k; R0402
R64, R66: 22R; R0402
R78, R82: 100k; R0402
R80: 10R; R0402
R83, R87: 200k_1%; R0402
S1, S2, S3, S4, S5, S6: 323030226; SHIELD_CLIP
TP1, TP2, TP3, TP4, TP5, TP6, TP7, TP8, TP9, TP10, TP14: TEST-POINT-35; TP_3535
TP15: TEST-POINT'4545'; TP-D45MIL
U1: SX1302IMLTRT; QFN68-0.35-7X7X0.75MM
U2, U8, U10: HDF866A3-S6; FILTER6P-1.1-3X3X1.3MM
U3, U4: DNP; SOT-23-5
U5, U7: SX1250IMLTRT; QFN24G-0.5-4X4MM
U6: MP2161GJ; TSOT23-8
U9: SKY66420-11; MODULE16P-0.5-3X3X0.75MM
U11: SX1262IMLTRT; QFN24G-0.5-4X4MM
U12: STM32L412K8U6; UFQFPN32-0.5-5X5MM
U13: STTS751; UDFN-6L
X1: DSB221SDN; X4-SMD-2.5X2.0X1.0MM
X3: 32.768kHz; X2-SMD-3.2X1.5X0.55MM

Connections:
32MHZ: R6.2, R9.2, R37.2, X1.3 (OUT)
1302_CS: R33.2, R43.1, U1.1 (HOST_CSN), U12.10 (PA4)
1302_RESET: C1.2, D7.-, R1.2, U1.7 (RESET), U12.8 (PA2)
1302_RESET_HOST: D7.+, R59.1
CONFIG_OK: R31.1, U1.66 (GPIO0)
DM: J1.36, R66.1
DP: J1.38, R64.1
FEM_CS: R14.2, R34.1, U1.10 (RADIO_CTRL0), U3.3 (CE)
FEM_PA_ON: R15.2, U1.16 (RADIO_CTRL4)
GND: ANT1.GND1, ANT1.GND2, ANT2.GND1, ANT2.GND2, C2.1, C3.1, C5.1, C7.1, C9.1, C12.1, C13.1, C15.1, C16.1, C17.1, C18.1, C19.1, C20.1, C21.1, C22.1, C23.1, C24.1, C25.1, C26.1, C27.1, C28.1, C29.1, C30.1, C31.1, C32.1, C33.1, C34.1, C35.1, C36.1, C37.1, C39.1, C40.1, C41.1, C42.1, C43.1, C44.1, C45.1, C46.1, C47.1, C48.1, C49.1, C50.1, C51.1, C52.1, C55.1, C56.1, C57.1, C58.1, C60.2, C61.2, C62.1, C63.2, C65.2, C67.2, C69.1, C70.1, C71.1, C72.1, C73.2, C74.2, C76.1, C77.2, C78.2, C80.1, C81.2, C82.2, C83.1, C84.2, C85.1, C86.1, C87.1, C88.1, C89.1, C90.1, C92.1, D1.-, D2.-, D3.-, D4.-, D5.1, D6.1, J1.4 (GND), J1.9 (GND), J1.15 (GND), J1.18 (GND), J1.21 (GND), J1.26 (GND), J1.27 (GND), J1.29 (GND), J1.34 (GND), J1.35 (GND), J1.37 (GND), J1.40 (GND), J1.43 (GND), J1.50 (GND), J1.S1 (GND), J1.S2 (GND), Q10.2 (S), R1.1, R4.1, R11.1, R12.1, R17.2, R53.1, R53.2, R54.1, R54.2, R55.1, R55.2, R57.2, R73.1, R74.1, R74.2, R87.1, S1.S1, S1.S2, S1.S3, S1.S4, S1.S5, S2.S1, S2.S2, S2.S3, S2.S4, S2.S5, S3.S1, S3.S2, S3.S3, S3.S4, S3.S5, S4.S1, S4.S2, S4.S3, S4.S4, S4.S5, S5.S1, S5.S2, S5.S3, S5.S4, S5.S5, S6.S1, S6.S2, S6.S3, S6.S4, S6.S5, TP3.T, U1.6 (GND), U1.9 (GND), U1.15 (GND), U1.24 (GND), U1.25 (GND), U1.39 (GND), U1.46 (GND), U1.55 (GND), U1.62 (GND), U1.69 (GND), U2.1 (GND), U2.3 (GND), U2.4 (GND), U2.6 (GND), U3.2 (VSS), U4.2 (VSS), U5.7 (GND), U5.20 (GND), U5.PAD, U6.4 (PGND), U6.6 (AGND), U7.7 (GND), U7.20 (GND), U7.PAD, U8.1 (GND), U8.3 (GND), U8.4 (GND), U8.6 (GND), U9.10 (GND), U9.12 (GND), U9.17 (EPAD), U10.1 (GND), U10.3 (GND), U10.4 (GND), U10.6 (GND), U11.2 (GND), U11.5 (GND), U11.8 (GND), U11.20 (GND), U11.PAD, U12.16 (VSS), U12.32 (VSS), U12.PAD, U13.4 (ADDR/!THERM), U13.5 (GND), X1.2 (GND)
HOST_CS0: J1.51, R43.2
HOST_CS1: J1.25, R51.2
HOST_IO1: J1.33, R61.2
HOST_IO2: J1.31, R63.2
HOST_IO3: J1.23
HOST_IO4: J1.8, R67.2
HOST_IO5: J1.10, R60.2
HOST_IO6: J1.12
HOST_MISO: R39.1, R44.2
HOST_MOSI: J1.49, R46.2
HOST_RST: J1.22, R59.2, R77.2
HOST_SCK: J1.45, R49.2
I2C_SCL: R68.2, R76.1, R81.1, U12.29 (PB6), U13.1 (SCL)
I2C_SDA: R58.2, R70.1, R75.1, U12.30 (PB7), U13.6 (SDA)
MCU_RESET: C85.2, R71.2, R77.1, TP5.T, U12.4 (NRST)
MISO: R44.1, R45.1, U1.2 (HOST_MISO), U11.16 (MISO)
MISO_A: U1.42 (RADIO_A_MISO), U5.16 (MISO)
MISO_B: U1.33 (RADIO_B_MISO), U7.16 (MISO)
MOSI: R5.2, R40.2, R46.1, R48.1
MOSI_A: U1.67 (RADIO_A_MOSI), U5.17 (MOSI)
MOSI_B: U1.19 (RADIO_B_MOSI), U7.17 (MOSI)
unnamed: C11.2, U9.2 (RX)
unnamed: TP15.T, U6.1 (PG)
unnamed: C8.1, R11.2, R52.2, U8.5 (OUT)
unnamed: C2.2, L11.2, R52.1, U8.2 (IN)
unnamed: C11.1, R13.2, U2.2 (IN)
unnamed: C4.2, U9.1 (TX)
unnamed: C68.1, C74.1, C75.2
unnamed: C65.1, L18.2, R36.2, U11.1 (VDD_IN)
unnamed: C66.2, R37.1
unnamed: L5.1, U6.3 (SW)
unnamed: R83.1, R87.2, U6.7 (FB)
unnamed: R3.1, R4.2, X1.1 (ENABLE)
unnamed: C14.1, U5.3 (XTA)
unnamed: C62.2, L4.1, R3.2, X1.4 (VDD)
unnamed: R5.1, U1.3 (HOST_MOSI)
unnamed: D4.+, R47.2
unnamed: R10.1, U1.4 (HOST_SCK)
unnamed: R82.2, U6.8 (EN)
unnamed: R8.1, U4.3 (CE)
unnamed: C14.2, R6.1
unnamed: L6.2, U5.8 (DCC_SW)
unnamed: C34.2, L6.1, L7.2, U5.6 (VREG)
unnamed: C64.1, C82.1, L24.2
unnamed: R19.1, U1.34 (RADIO_B_CLK_I)
unnamed: C16.2, R14.1, U9.4 (CSD)
unnamed: C38.1, U7.3 (XTA)
unnamed: C36.2, C37.2, L9.2, U5.1 (VR_PA)
unnamed: C38.2, R9.1
unnamed: L14.2, U7.8 (DCC_SW)
unnamed: C46.2, L14.1, L15.2, U7.6 (VREG)
unnamed: C54.2, L11.1
unnamed: C7.2, C53.2, C54.1, L10.2
unnamed: C4.1, C8.2, R12.2
unnamed: C17.2, R15.1, U9.5 (CPS)
unnamed: C18.2, R16.1, U9.6 (CTX)
unnamed: R17.1, U1.20 (SP_VALID)
unnamed: R18.1, U1.32 (RADIO_B_IQ3)
unnamed: R20.1, U1.35 (RADIO_B_IQ0)
unnamed: R24.1, U1.41 (RADIO_A_IQ3)
unnamed: R21.1, U1.36 (RADIO_B_IQ1)
unnamed: R22.1, U1.37 (RADIO_B_IQ4)
unnamed: R23.1, U1.38 (RADIO_B_IQ2)
unnamed: R25.1, U1.43 (RADIO_A_CLK_I)
unnamed: R26.1, U1.44 (RADIO_A_IQ0)
unnamed: R27.1, U1.45 (RADIO_A_IQ1)
unnamed: R28.1, U1.48 (RADIO_A_IQ4)
unnamed: R29.1, U1.49 (RADIO_A_IQ2)
unnamed: D3.+, R32.2
unnamed: D2.+, R31.2
unnamed: D1.+, R30.2
unnamed: Q8.1 (G), Q10.3 (D), R78.2
unnamed: C1.1, R80.1
unnamed: L1.1, U9.16 (VCC1)
unnamed: L2.1, L8.1, U9.13 (PA_OUT)
unnamed: C56.2, C57.2, L8.2, L16.1
unnamed: C58.2, L16.2, U9.11 (TX_IN)
unnamed: C59.2, C60.1, L17.1, U9.9 (ANT)
unnamed: C61.1, C91.1, L17.2, L24.1
unnamed: C66.1, U11.3 (XTA)
unnamed: ANT1.D, C64.2, D5.2
unnamed: R35.2, R62.1, R69.2, U10.2 (IN)
unnamed: C63.1, L18.1, L20.1, U11.7 (VREG)
unnamed: R35.1, U9.7 (LNA_IN), U10.5 (OUT)
unnamed: L20.2, U11.9 (DCC_SW)
unnamed: J1.47, R39.2
unnamed: R40.1, U11.17 (MOSI)
unnamed: R41.1, U11.18 (SCK)
unnamed: C6.1, C10.1, C75.1, R13.1, U2.5 (OUT)
unnamed: R69.1, U9.8 (RX_FLT)
unnamed: C78.1, C79.1, L21.2
unnamed: ANT2.D, C79.2, D6.2
unnamed: C59.1, C91.2
unnamed: C77.1, L21.1, R62.2
unnamed: R65.2, U13.2 (!EVENT)
unnamed: C52.2, FB1.1, L1.2, U9.15 (VCC0)
unnamed: R64.2, U12.22 (PA12)
unnamed: R66.2, U12.21 (PA11)
unnamed: C92.2, Q10.1 (G), R79.2
unnamed: R56.2, R57.1, U12.31 (BOOT0)
unnamed: R72.2, R73.2, U12.6 (PA0-CLK_IN)
unnamed: C81.1, U12.2 (PC14-OSC32_IN), X3.2
unnamed: C84.1, U12.3 (PC15-OSC32_OUT), X3.1
unnamed: J1.14, R76.2
unnamed: J1.16, R70.2
unnamed: J1.30, R81.2
unnamed: J1.32, R75.2
PPS: J1.19, TP2.T, U1.8 (PPS), U12.27 (PB4)
RADIO_A_CLK_32M: R25.2, R72.1, U5.14 (BUSY)
RADIO_A_CLK_O: R28.2, U5.11 (DIO5)
RADIO_A_CSN: U1.68 (RADIO_A_CSN), U5.19 (NSS)
RADIO_A_IQ_0: R26.2, U5.13 (DIO1)
RADIO_A_IQ_1: R27.2, U5.12 (DIO2)
RADIO_A_IQ_2: R29.2, U5.5 (DIO3)
RADIO_A_IQ_3: R24.2, U5.21 (DIO4)
RADIO_A_RESET: U1.13 (RADIO_CTRL3), U5.15 (NRESET)
RADIO_A_RFIN: C6.2, L12.2, U5.23 (RFI_N)
RADIO_A_RFIP: C5.2, L12.1, U5.22 (RFI_P)
RADIO_B_CLK_32M: R19.2, U7.14 (BUSY)
RADIO_B_CLK_O: R22.2, U7.11 (DIO5)
RADIO_B_CSN: U1.18 (RADIO_B_CSN), U7.19 (NSS)
RADIO_B_IQ0: R20.2, U7.13 (DIO1)
RADIO_B_IQ_1: R21.2, U7.12 (DIO2)
RADIO_B_IQ_2: R23.2, U7.5 (DIO3)
RADIO_B_IQ_3: R18.2, U7.21 (DIO4)
RADIO_B_RESET: U1.28 (RADIO_CTRL9), U7.15 (NRESET)
RADIO_B_RFIN: C10.2, L13.2, U7.23 (RFI_N)
RADIO_B_RFIP: C9.2, L13.1, U7.22 (RFI_P)
RFO: C53.1, L9.1, L10.1, U5.24 (RFO)
RX_ON: R32.1, U1.59 (GPIO4)
SCK: R10.2, R41.2, R49.1, R50.1
SCK_A: U1.65 (RADIO_A_SCK), U5.18 (SCK)
SCK_B: U1.21 (RADIO_B_SCK), U7.18 (SCK)
STM32_MISO: R45.2, U12.12 (PA6)
STM32_MOSI: R48.2, U12.13 (PA7)
STM32_SCK: R50.2, U12.11 (PA5)
SWCLK: TP7.T, U12.24 (PA14)
SWDIO: TP8.T, U12.23 (PA13)
SX1261_BUSY: R67.1, U11.14 (BUSY), U12.9 (PA3)
SX1261_CS: R42.1, R51.1, U11.19 (NSS), U12.14 (PB0)
SX1261_IO1: R61.1, U1.54 (GPIO7), U11.13 (DIO1), U12.15 (PB1)
SX1261_IO2: R63.1, U11.12 (DIO2)
SX1261_IO3: TP9.T, U11.6 (DIO3)
SX1261_RFIN: C68.2, L22.2, U11.22 (RFI_N)
SX1261_RFIP: C73.1, L22.1, U11.21 (RFI_P)
SX1261_RST: R38.1, R60.1, U11.15 (NRESET), U12.18 (PA8)
SX1302_GPIO8: U1.53 (GPIO8), U12.26 (PB3)
TX_ON: R30.1, U1.63 (GPIO2)
TX_RX_SW: R16.2, U1.12 (RADIO_CTRL2)
VCCIO: C3.2, C19.2, C20.2, C25.2, C28.2, C41.2, C42.2, C45.2, C47.2, C76.2, C80.2, C83.2, C86.2, C87.2, C88.2, C89.2, C90.2, Q8.3 (D), R33.1, R34.2, R56.1, R58.1, R65.1, R68.1, R71.1, R80.2, TP1.T, U1.14 (VCC_IO), U1.30 (VCC_IO), U1.47 (VCC_IO), U1.61 (VCC_IO), U12.1 (VDD), U12.5 (VDDA), U12.17 (VDD), U13.3 (VDD)
VCC_1V2: C12.2, C13.2, C23.2, C24.2, C29.2, C40.2, C43.2, C44.2, C71.2, C72.2, L5.2, R79.1, R83.2, TP14.T, U1.5 (VCC_CORE), U1.23 (VCC_CORE), U1.40 (VCC_CORE), U1.56 (VCC_CORE), U6.5 (OUT)
VCC_FEM: C26.2, C27.2, C49.2, C50.2, C51.2, C55.2, FB1.2, L2.2, R2.2, TP6.T, U3.5 (VOUT)
VCC_RADIO: C21.2, C32.2, C33.2, C35.2, C39.2, C48.2, C67.1, L4.2, L7.1, L15.1, R7.2, R36.1, R38.2, R42.2, TP10.T, U4.5 (VOUT), U5.2 (VDD_IN), U5.9 (VBAT_RF), U5.10 (VBAT_DIO), U7.2 (VDD_IN), U7.9 (VBAT_RF), U7.10 (VBAT_DIO), U11.10 (VBAT), U11.11 (VBAT_IO)
VIN: C15.2, C22.2, C30.2, C31.2, C69.2, C70.2, J1.2 (3V3), J1.24 (3V3), J1.39 (3V3), J1.41 (3V3), J1.52 (3V3), Q8.2 (S), R2.1, R7.1, R8.2, R47.1, R78.1, R82.1, TP4.T, U3.1 (VIN), U4.1 (VIN), U6.2 (VIN)

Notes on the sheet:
V1.0
Initial Release
2020/01/02
Vincent
50ohm Impedence
3.3V
300mA
1.2V
500mA
100mA
USB
868
915
SPI
For Power-up delay
V1.1
Add power up delay circuit at VCCIO
Add power up reset circuit for SX1302
Change pins refer to Semtech V3 Schematic
2021/02/18

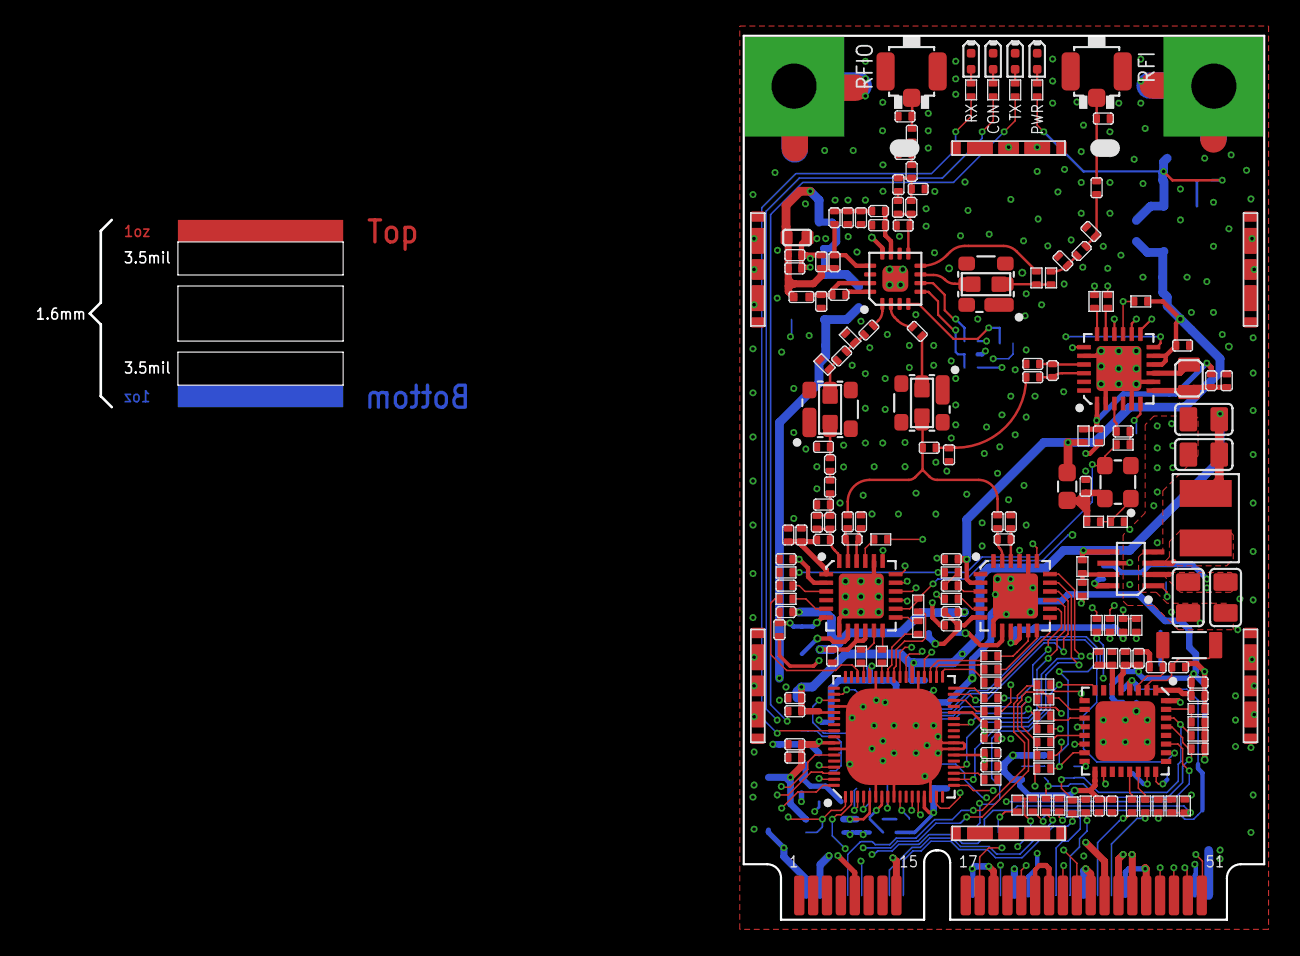
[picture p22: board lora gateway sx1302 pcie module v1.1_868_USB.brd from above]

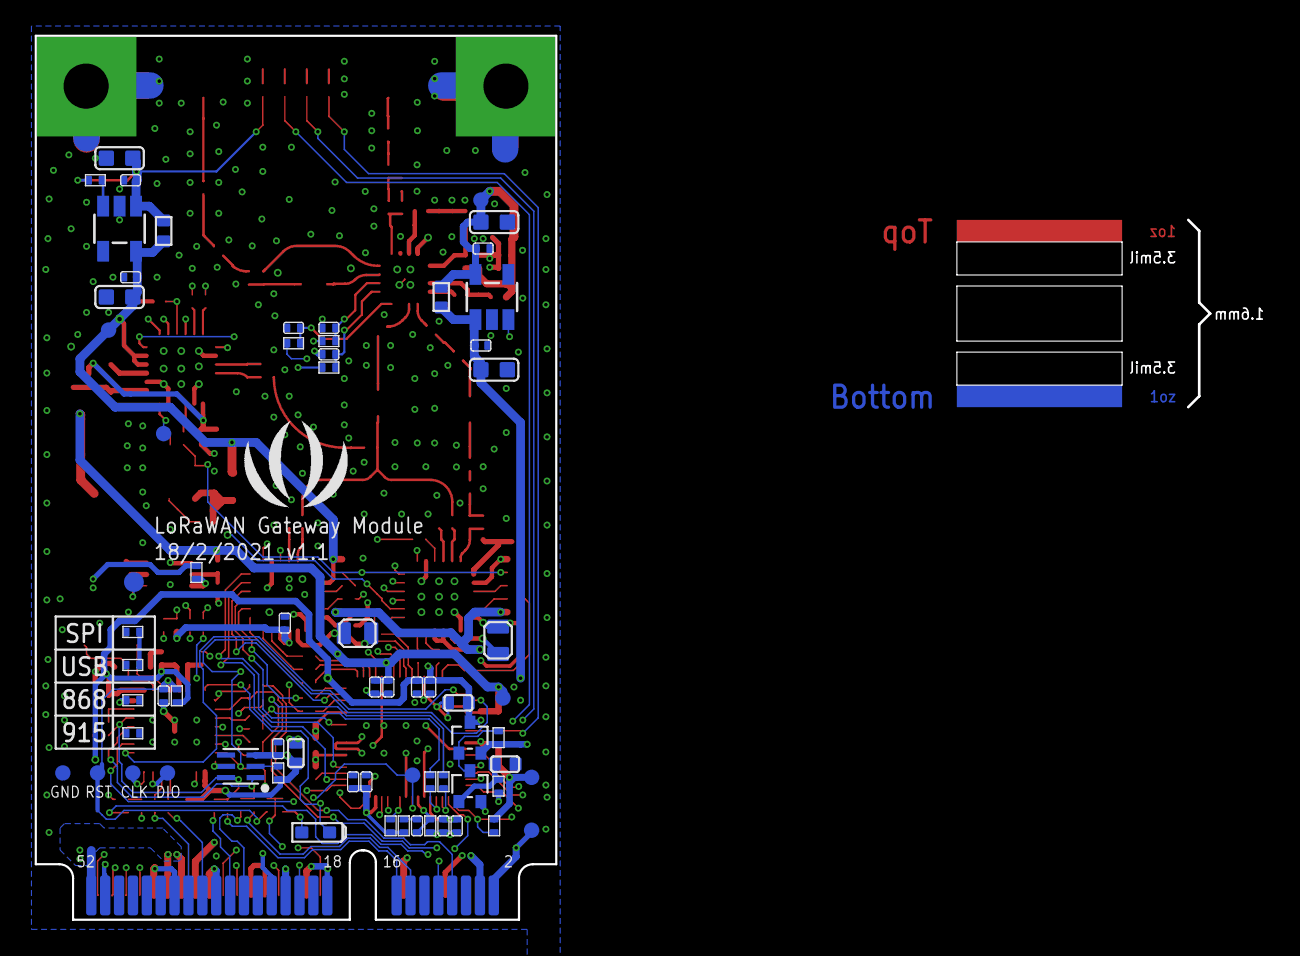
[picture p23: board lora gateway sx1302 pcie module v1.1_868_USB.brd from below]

Board: 4 copper layers, 30.0 x 51.0 mm, 244 parts (68 on the bottom side), 162 nets.

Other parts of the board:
U$45: SEEED-SILK-TNAME-280*268MIL

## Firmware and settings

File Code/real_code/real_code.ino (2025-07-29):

#include <Servo.h>
#include "MAX31855.h"

Servo theservo;

float wiper_to_angle_scale = 0;
float wiper_to_angle_offset = 0;

float reading;

const int servo_pin = 28;
const int servo_feedback_pin = A1;
const int set_pin = 0;
const int store1_pin = 7;
const int store2_pin = 6;
const int warning_light_pin = 3;
const int fader_pin = A0; // set this up
const int big_led_dimming_pin = 29; // set this up
const int SPI_CHIP_SELECT = 1;
const int SPI_MISO = MISO;
const int SPI_SYSTEM_CLOCK = SCK;

MAX31855_Class MAX31855; // (LED temperature monitoring chip)

float store1;
float store2;

bool do_movement_limits = true;
int upper_movement_limit = 170;
int lower_movement_limit = 10;

float read_analogue_input_avg(int delay_time=5, int readings=50) {
  float avg_read;
  int i;

  avg_read = analogRead(servo_feedback_pin);
  for (i=1; i<readings; i++) {
    avg_read = (avg_read + analogRead(servo_feedback_pin)) / 2;
    delay(delay_time);
  }
  return avg_read;
}

float wiper_to_angle(float analogue_input) {
  return (analogue_input - wiper_to_angle_offset) / wiper_to_angle_scale ;
}


void setup() {
  digitalWrite(big_led_dimming_pin, HIGH); // driving it high will make the output of the optocoupler be low in theory so the led driver is set to 0%
  float wiper_at_60;
  float wiper_at_120;
  int i;

  theservo.attach(servo_pin);
  Serial.begin(115200);
  pinMode(set_pin, INPUT_PULLUP);
  pinMode(store1_pin, INPUT_PULLUP);
  pinMode(store2_pin, INPUT_PULLUP);
  pinMode(servo_feedback_pin, INPUT_PULLUP);
  pinMode(warning_light_pin, OUTPUT);

  while (!MAX31855.begin(SPI_CHIP_SELECT) || (!digitalRead(set_pin) && !digitalRead(store1_pin) && !digitalRead(store2_pin))) {
    Serial.println("Failed to set up MAX31855 temperature monitoring, retrying in 3 seconds or press all 3 buttons to override, DOING THIS PUTS YOU AT RISK OF THE LED OVERHEATING AND DYING!!!!!!!!");
    delay(3000);
  }

  theservo.write(59);
  delay(800);
  theservo.write(60);
  delay(150);
  wiper_at_60 = read_analogue_input_avg(5, 200);

  theservo.write(121);
  delay(800);
  theservo.write(120);
  delay(150);
  wiper_at_120 = read_analogue_input_avg(5, 200);

  for (i=0; i<3; i++) {
    theservo.write(59);
    delay(800);
    theservo.write(60);
    delay(150);
    wiper_at_60 = (wiper_at_60 + read_analogue_input_avg(5, 150)) / 2;

    theservo.write(121);
    delay(800);
    theservo.write(120);
    delay(150);
    wiper_at_120 = (wiper_at_120 + read_analogue_input_avg(5, 150)) / 2;
  }

  Serial.print("60º: ");
  Serial.println(wiper_at_60);
  Serial.print("120º: ");
  Serial.println(wiper_at_120);

  wiper_to_angle_scale = (wiper_at_120 - wiper_at_60) / (120-60);
  wiper_to_angle_offset = wiper_at_60 - 60 * wiper_to_angle_scale;

  Serial.print("Scale: ");
  Serial.println(wiper_to_angle_scale);
  Serial.print("Offset: ");
  Serial.println(wiper_to_angle_offset);

  //theservo.write(0);
  delay(2000);

  //for (i=0; i<=180; i += 5) {
  //  theservo.write(i);
  //  delay(100);
  //  reading = read_analogue_input_avg(6, 200);
  //  Serial.print(i);
  //  Serial.print("º is read as ");
  //  Serial.print(wiper_to_angle(reading));
  //  Serial.println("º");
  //}
  theservo.detach();
}


float angle;

void loop() {
  int ambient_temp = MAX31855.readAmbient();
  int probe_temp = MAX31855.readProbe();
  int fault_code = MAX31855.fault();

  // temperature management
  if (probe_temp >= 105) {
    digitalWrite(big_led_dimming_pin, HIGH); // If temperature's very too hot, turn off LED to protect it
    int brightness_multiplier = 0;
  }
  else if (probe_temp >= 100) {
    int brightness_multiplier = 0.2;
  }
  else if (probe_temp >= 95) {
    int brightness_multiplier = 0.45;
  }
  else if (probe_temp >= 90) {
    int brightness_multiplier = 0.7;
  }
  else if (probe_temp >= 85) {
    int brightness_multiplier = 0.9;
  }
  else {
    brightness_multiplier = 1;
  }

  if (brightness_multiplier != 1) {
    Serial.print("Thermal throttling, LED is ");
    Serial.print(probe_temp);
    Serial.println(" celcius");
    analogWrite(warning_light_pin, 255 * (1-brightness_multiplier));
  }


  // servo management
  reading = read_analogue_input_avg(1, 10);
  angle = wiper_to_angle(reading);

  if (do_movement_limits) {
    if ((angle <= lower_movement_limit || angle >= upper_movement_limit) && !theservo.attached()) {
        theservo.write(angle);
        theservo.attach(servo_pin);
        digitalWrite(warning_light_pin, HIGH);
        Serial.println("hey!");
      }

    if (angle <= lower_movement_limit+10) {
      theservo.write(angle + 2);
    }
    else if (angle >= upper_movement_limit-10) {
      theservo.write(angle - 5);
    }

    if ((lower_movement_limit+2 <= angle) && (angle <= upper_movement_limit-5) && theservo.attached()) {
      theservo.write(angle);
      theservo.detach();
      digitalWrite(warning_light_pin, LOW);
      Serial.println("yay");
    }
  }


  if (digitalRead(store1_pin) == 0  && !(digitalRead(store2_pin) == 0) {
    if (digitalRead(set_pin) == 0) {
      store1 = wiper_to_angle(read_analogue_input_avg(2, 50));
    }
    else {
      if (!theservo.attached()) {
        theservo.attach(servo_pin);
      }
      theservo.write(store1);
      delay(300);
      theservo.detach();
    }
  }
  else if (digitalRead(store2_pin) == 0 && !(digitalRead(store2_pin) == 0)) {
    if (digitalRead(set_pin) == 0) {
      store2 = wiper_to_angle(read_analogue_input_avg(2, 50));
    }
    else {
      if (!theservo.attached()) {
        theservo.attach(servo_pin);
      }
      theservo.write(store2);
      delay(300);
      theservo.detach();
    }
  }

  Serial.print(angle);
  Serial.println("º");


  // fader management

  fader_reading = analogRead(fader_pin); // 0-255 hopefully
  digitalWrite(big_led_dimming_pin, (fader_reading * brightness_multiplier) / 1) + 255;

}

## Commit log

2025-05-20 added pcb files
    [Grove - Vision AI Module V2.kicad_pcb, Grove - Vision AI Module V2.kicad_sch, Grove_Vision_AI_V2_BOM.xlsx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]
2025-05-20 new meanwell 5v psu instead of mystery box
    [PCB.kicad_sch]
2025-05-21 made pcb better or something, oh yeah and i added the meanwell led driver as a schematic symbol
    [PCB.kicad_sch]
2025-05-24 yippee done the lens holder!!!!
2025-05-26 led platform
2025-05-28 yay yummy servo code, it currently calibrates itself and then deactivates the servo to let you move it manually, and giving serial output of the rotation based on the resistance of the potentiometer 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
2025-05-28 it's a little wonky but it kind of stores positions? it likes to get stuck on the moving the motor and keeps thinking the pin is pressed even though it's not
    [servo_stuff.ino]
2025-05-29 attempted to fix some of the weirdness with rotation limiting - it no longer randomly decides to jump up, and there's a little less bouncing at the lower limit
    [servo_stuff.ino]
2025-05-30 PCB resistor
    [PCB.kicad_sch]
2025-06-08 add libraries that i had but didn't add to git
    [MAX6675.step]
2025-06-20 add all the changes i've made, sorry for not gitting it bit by bit
    [691137710002+%28rev1%29 terminal block.stp, PCB.kicad_pcb, PCB.kicad_sch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]
2025-06-23 fix malformed pcb file
    [PCB.kicad_sch]
2025-06-29 uhh did stuff by the looks of it
    [PCB.kicad_pcb, PCB.kicad_sch]
2025-07-15 add slight pcb changes
    [PCB.kicad_pcb, PCB.kicad_sch]
2025-07-24 add changed files
    [PCB.kicad_pcb, PCB.step]
2025-07-24 add wiring diagram
2025-07-25 add BoM
2025-07-25 add links to BoM because ag why didn't it just have that in the converter
2025-07-25 add bunch of files and did some code
    [BoM.csv, BoM.xlsx, Electronics Box.step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]
2025-07-29 bom with links because excel silly
    [BoM.csv]
2025-08-14 updated readme bom to reflect the cheaper led i actually bought
2025-08-14 Update BoM.csv to reflect the cheaper led i actually bought
    [BoM.csv]
